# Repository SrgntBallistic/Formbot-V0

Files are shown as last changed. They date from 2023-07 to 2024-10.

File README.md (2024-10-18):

# Formbot-V0

Details/Documentation for the Formbot V0 Kit

## Detailed Review

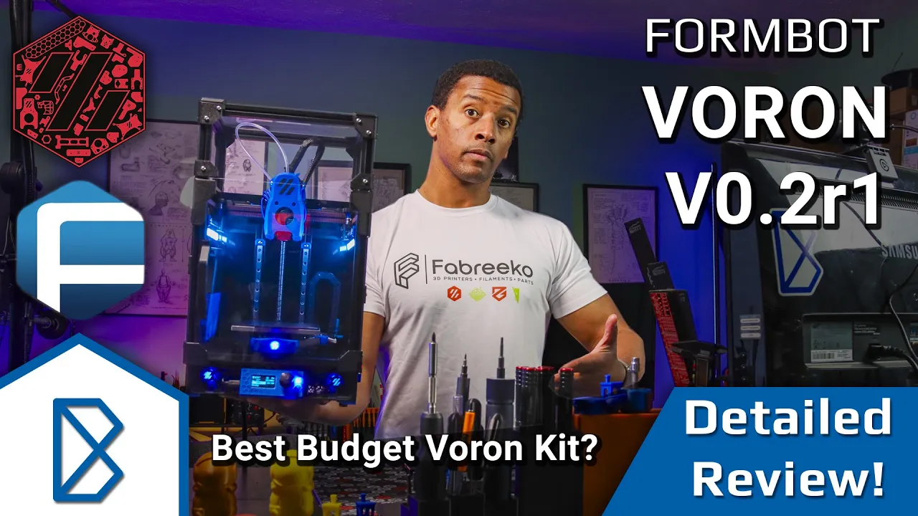
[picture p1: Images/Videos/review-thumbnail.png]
Formbot V0 Kit Review (https://www.youtube.com/watch?v=wvUrcIFF510)

<https://www.youtube.com/watch?v=wvUrcIFF510>

## Stream Series

Check out my full build stream series here:
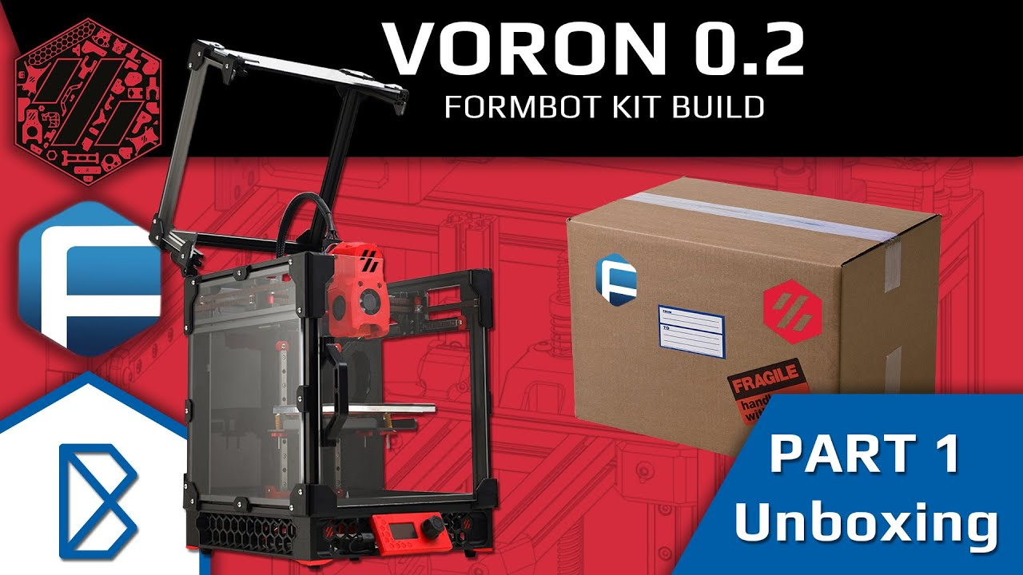
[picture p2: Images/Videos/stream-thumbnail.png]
Formbot V0 Kit Stream Series (https://www.youtube.com/playlist?list=PLwWNdxHVFVf1DbI2nGngUB0O9TWeXn2Sx)

<https://www.youtube.com/playlist?list=PLwWNdxHVFVf1DbI2nGngUB0O9TWeXn2Sx>

## Voron DB Entry

Voron DB Entry (https://vorondb.com/printer/V0-3207)
<https://vorondb.com/printer/V0-3207>

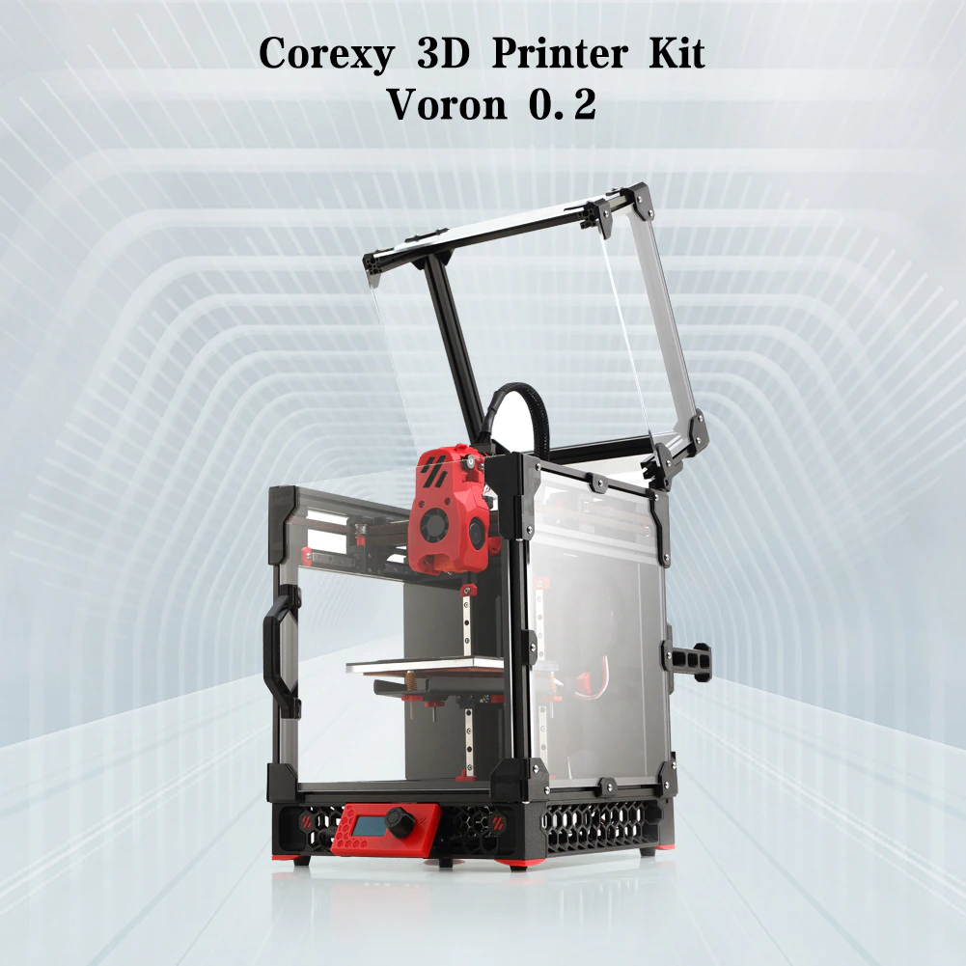
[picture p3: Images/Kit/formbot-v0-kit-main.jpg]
Formbot V0 Kit


## Features

Note: For each of the features/mods please make sure to go to the repective documentation to download and print all of the necessary STLs.

- Kirigami Bed Frame
- BTT Pi V1.2
- BTT SKR Pico
- BTT V0 Display
- CHC V6 Hotend (Upgradeable to Dragon/HF)
- Double Sided PEI Sheet
- Crimped Wiring Looms
- Moons Motors
- Stainless Steel Rails
- MIC6 Cast Aluminum Build Plate
- Polycarbonate Panels
- Gates Belts
- Vivedino 60W Silicone Bed Heater
- Stainless Steel Hardware
- Umbilical Board + Harness
- **NOT** Makerbeam XL Extrusion!!! LDO Style
- Meanwell 150W PSU

Aliexpress Listing: <https://s.click.aliexpress.com/e/_Dk19GYN>

Formbot Listing: <https://www.formbot3d.com/products/voron-v02-corexy-3d-printer-kit-with-high-quality-parts?DIST=RkFPFVk%3D>

Disclaimer: Purchases made through some store links may provide some compensation to Ballistic Tech.

## Helpful info

Most of this is set in the `printer.cfg` file I've provided:
<https://github.com/SrgntBallistic/Formbot-V0/blob/v0.2/Firmware/bigtreetech-skr-pico-v1.0.cfg>

Replace the entire contents of your `printer.cfg` file with the contents of the file linked above. Follow the instructions in the comments to add the serial Ids for your MCU and Display.

### My Config Backup

** WARNING: ** I do not advice copying my entire config setup. I'm using a lot of custom macros and plugins. I do not guarantee this config is in a working state!

<https://github.com/SrgntBallistic/blue-v0.2-backup-config>

### Motor Models

Helpful for the Autotune TMC Klipper Plugin

- A/B - MS14HS5P4150-11
- Z - LE174S-T0808-200-0-S-065
- E - CSE14HRA1L410A-01

Link: <https://github.com/andrewmcgr/klipper_tmc_autotune>

### Max Motor Currents

- A/B - 1.5A
- Z - 0.65A
- E - 1.0A

### Motor drawings with current ratings

A/B - <https://github.com/SrgntBallistic/Formbot-V0/blob/v0.2/Images/Motors/a-b-motors-drawing.jpg>

Z - <https://github.com/SrgntBallistic/Formbot-V0/blob/v0.2/Images/Motors/extruder-motor-drawing.jpg>

E - <https://github.com/SrgntBallistic/Formbot-V0/blob/v0.2/Images/Motors/extruder-motor-drawing.jpg>

### 65% Run Currents

Voron recommends 60-70% (0.6-0.7) to start
I chose 65%. Increase as needed but try to stay below 80-90%

Run Current = rated_motor_current x 0.707 x 0.65

Plug the max currents above into the equation with your desired percentage

- A/B - 0.65 x 0.707 x 1.5A = 0.69 (NICE!)
- Z - 0.65 x 0.707 x 0.65A = 0.3A
- E - 0.65 x 0.707 x 1.0A = 0.46A

### Thermistors

- Formbot Bed - "Generic 3950"
- Formbot V6 CHC Hotend - "ATC Semitec 104NT-4-R025H42G"
- Check Klipper docs for the correct sensor type based on your thermistor/hotend

### Extrusion Identification

All of the extrusions in the Formbot V0 kit are tapped on both ends. This means that using the V0 Manual extrusion identification diagrams can be a bit confusing. For 4 sets of extrusions where the manual differentiates them by tapped ends, you can consider those extrusions to be identical.

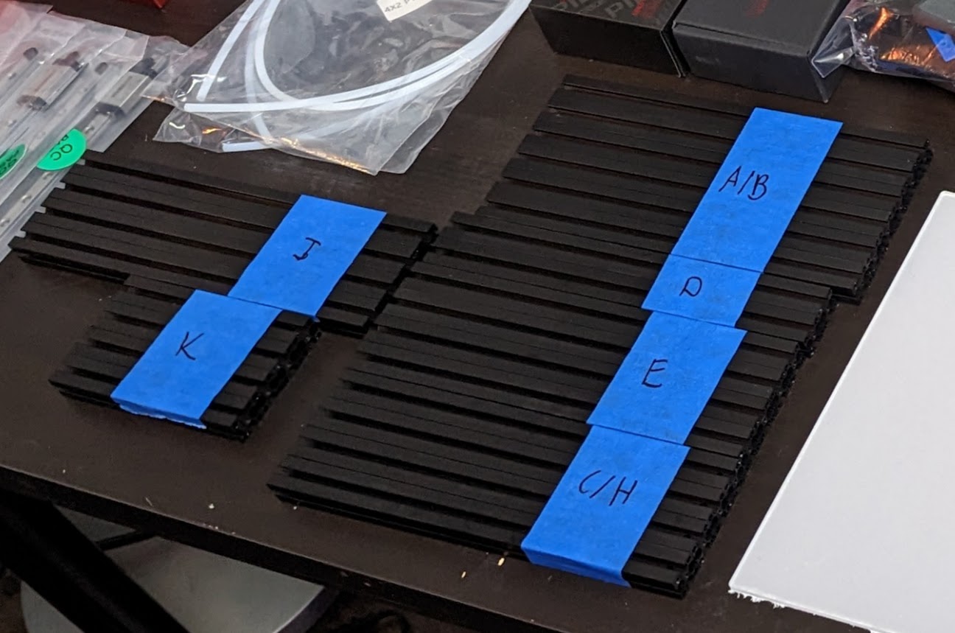
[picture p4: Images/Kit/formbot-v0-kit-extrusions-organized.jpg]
Extrusions Identification


#### Identical Extrusions

- A/B
- C/H

### No Drop Nuts

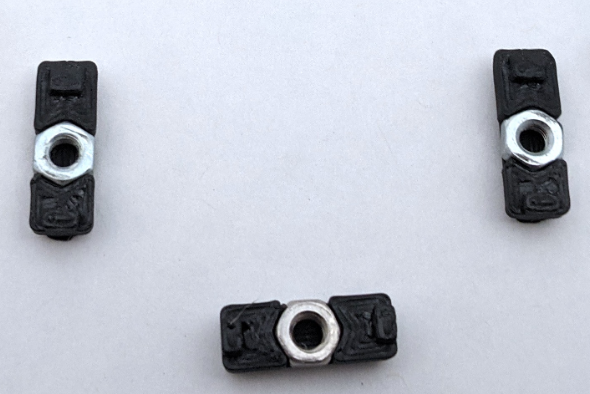
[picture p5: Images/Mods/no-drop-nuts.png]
No Drop Nuts


No drop nuts are very helpful for preventing preloaded M3 Hex Nuts from sliding around or falling out of the frame during assembly. They also allow you to pre align the nuts and hold them in place while you attatch parts to the frame.

The Formbot Extrusions are NOT MakerBeamXL profiles. They are closer to LDO's 1515 Extrusion. As such the no drop hex nut mods designed for LDO's kits work well with the Formbot kit.

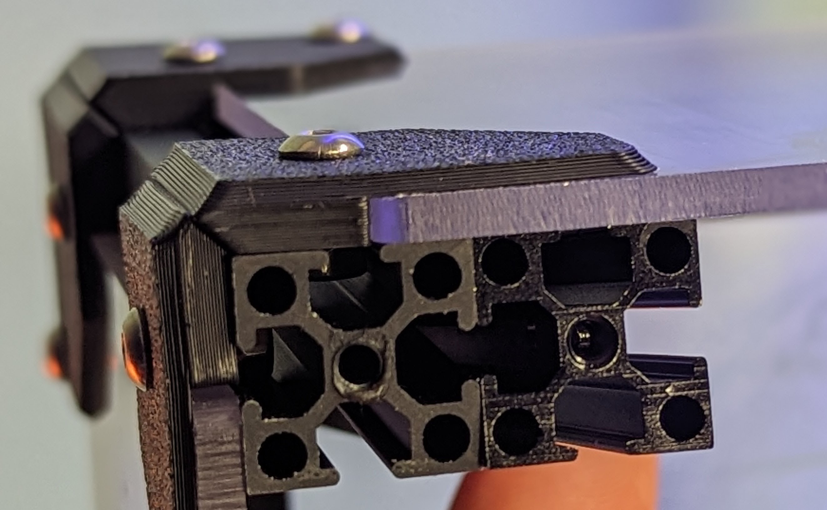
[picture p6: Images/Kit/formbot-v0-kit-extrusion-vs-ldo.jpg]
Formbot vs LDO Extrusion

Above: Left - Formbot Extrusion, Right - LDO Extrusion

#### Be Careful

I used them and found them very helpful. One big thing to note is that using the normal no drop nuts for the magnetic door latch can cause an issue. The spacing for these printed parts is such that using no drop carriers will cause them to be too far apart.

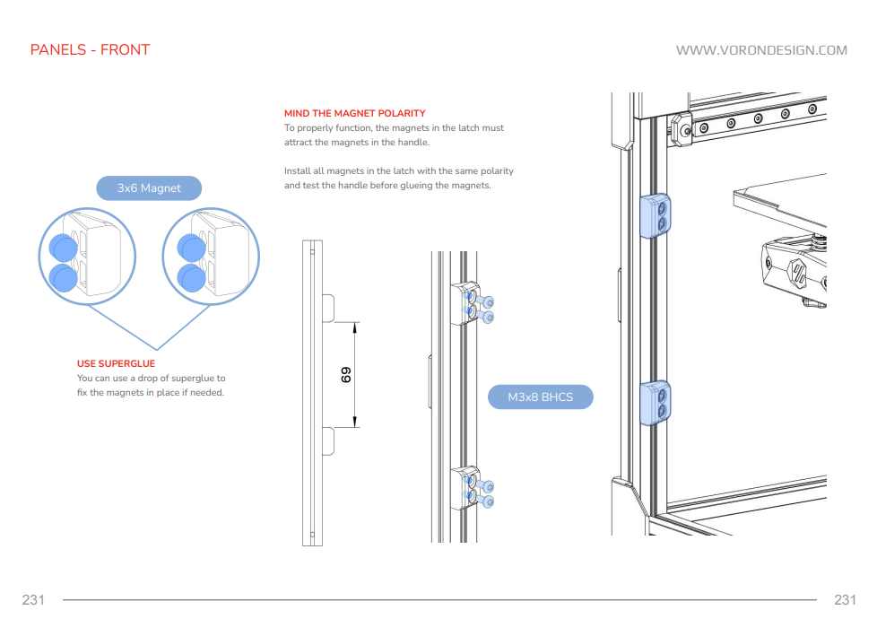
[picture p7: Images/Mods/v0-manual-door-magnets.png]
V0 Manual Door Latch


I used normal no drop nuts for these and had to essentially break apart the nut carriers to have them align with magnetic door latch parts.

There is a specific version of the No Drop Nut that is designed to be used here:

<https://github.com/VoronDesign/VoronUsers/blob/master/printer_mods/zruncho/V0_No_Drop_Nuts/stl/NoDropNut_Door_Latch_x2.stl>

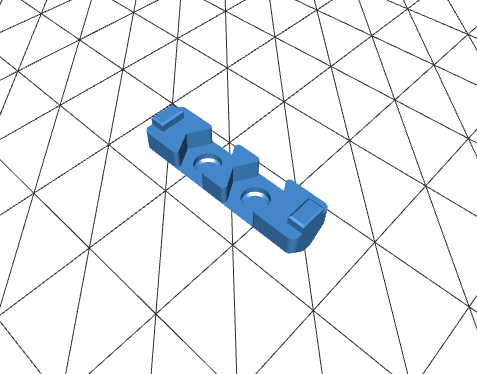
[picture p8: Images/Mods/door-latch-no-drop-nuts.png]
Door Latch No Drop Nuts


## Kirigami Bed

Kirigami Bed
GitHub: <https://github.com/christophmuellerorg/voron_0_kirigami_bed>

Manual: <https://github.com/Kagee/kirigami-bed-manual>

LDO Kirigami Docs: <https://www.ldomotion.com/p/guide/18295873486461670>

Remixed Formbot V0.2 Kirigami Frame Nutblock By @manisto: <https://www.printables.com/model/837960-kirigami-bed-nut-block-for-voron-v02>

Remixed Formbot V0.2 Kirigami Frame Chain Mount: **User Deleted. Need New Model**

The Formbot kit only comes with the Kirigami Frame. There's no LED/PCBs/Wago connectors, etc... included with the kit. You can source these yourself, find a partial wiring kit that includes them, or just leave them out and hard wire the bed components. See my My Mods section for the kit I bought.

The Kirigami bed frame is a great mod/upgarde that comes with the kit. It replaces multipe extrusions and printed pieces with a single rigid bed frame. The LDO Docs and Kirigami manual by Kagee provide some great info on general installation of the bed.

I had some trouble with the provided bed. I was able to get through all the issues with small DIY fixes. Other people have also noted they've run into these issues on the Voron Discord as well as the Kirigami GitHub. YMMV

## Issues

- Frame Thickness
  - My frame measured about 2.3-2.5mm
    - I think this is due to the thickness of the paint on the frame
  - Spec is 2mm, max tolerance of 0.2mm
  - Caused the frame to not fit the printed Kirigami "stealth" Parts
    - Stealth Nut Block
    - Steath Chain Mount
    - Can file the gaps in these parts or modify them in CAD and reprint if they don't fit
    - Can also use some of the legacy non stealth parts

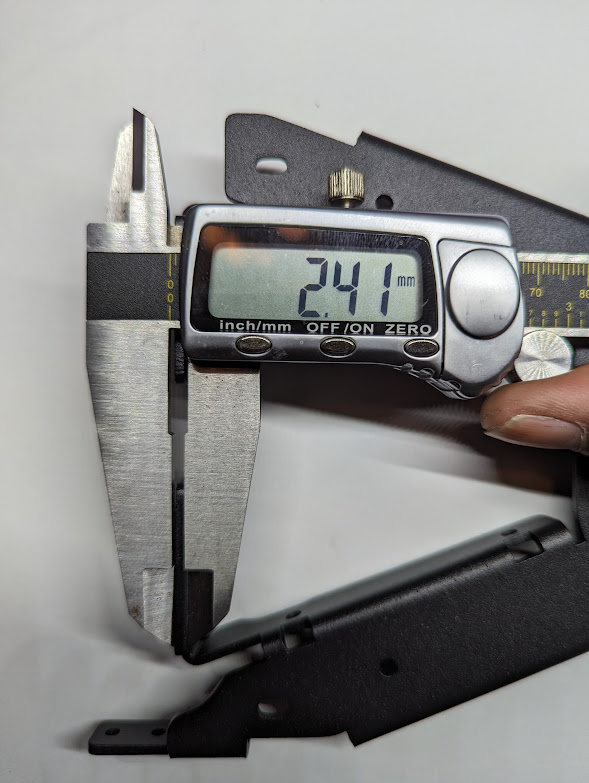
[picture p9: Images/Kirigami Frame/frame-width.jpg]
Kirigami Frame Thickness


For the chain mount Voron Discord/Printables user Tommy Vercetti remixed the part so it fits well on the Formbot frame

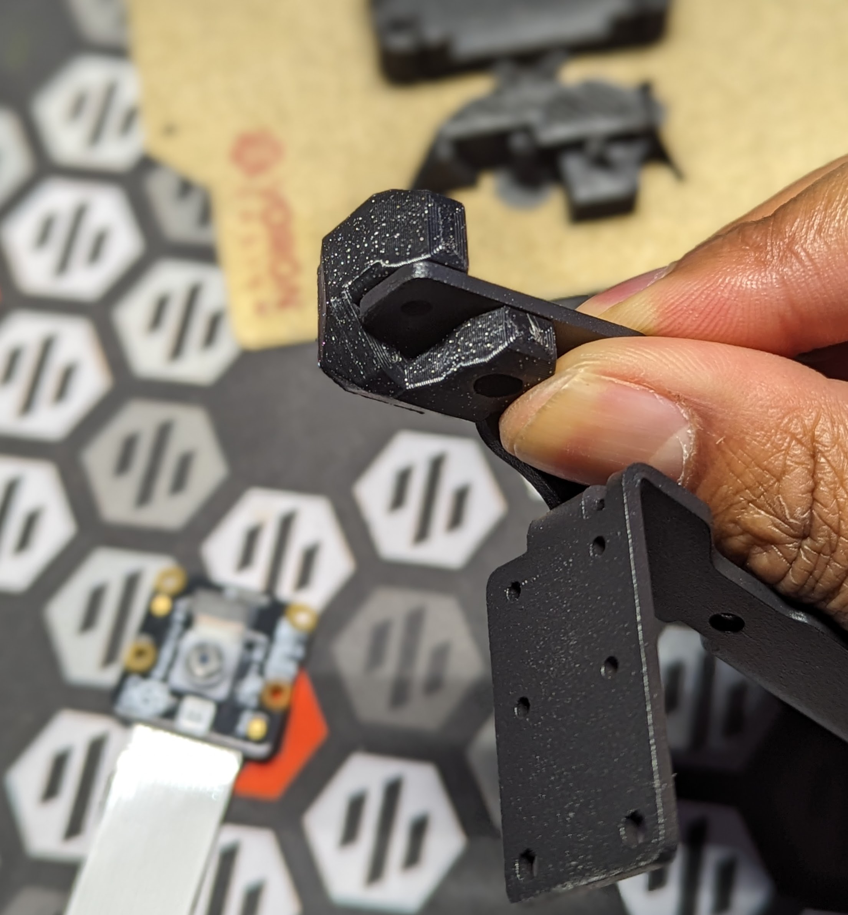
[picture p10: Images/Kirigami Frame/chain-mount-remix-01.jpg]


GitHub Issue: <https://github.com/christophmuellerorg/voron_0_kirigami_bed/issues/16>

- Frame holes
  - Again likely due to the thickness of the paint
  - Caused some slight over constraining of the frame when attached to the Z carriages
  - My mounting screws barely fit through the holes
  - No wiggle room to allow the frame and carriages to self align in a well enough that the frame and carriages would fall under their own weight
    - Didn't completely bind the frame movement
    - Just wasn't as smooth/free as after fixing
  - Compounded with the frame not fitting in the nut block well
  - Solved by filing out the holes in the frame
    - This reduced the constaining and allowed the bed to fall easily

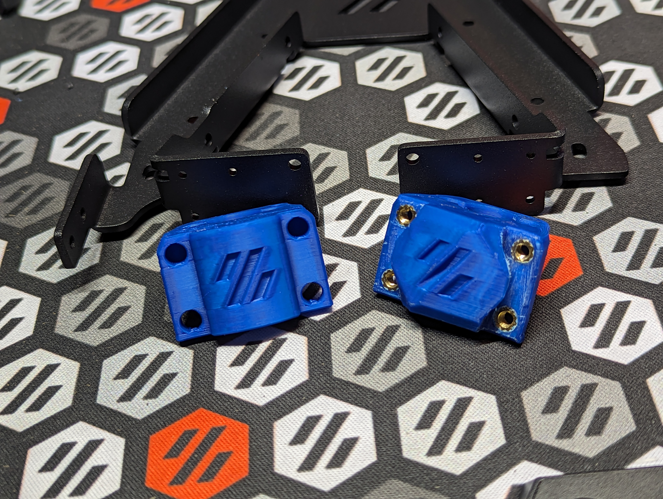
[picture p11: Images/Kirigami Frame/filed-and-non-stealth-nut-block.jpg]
Kirigami Frame Nutblocks


Non Stealth (Left) and Filed Stealth Nutblock (Right)

- Thermal Fuse Location
  - When I went to adjust the bed screws so they bed was just close enough to the nozzle I couldn't get the bed springs to compress enough
  - The thermal fuse was running into the frame
  - I could have reduced the Max Z so the bed wouldn't come up as high after homing
  - But didn't want to lose any Z height
  - Solved by filing away a tiny bit of material on the frame where the fuse was interferring

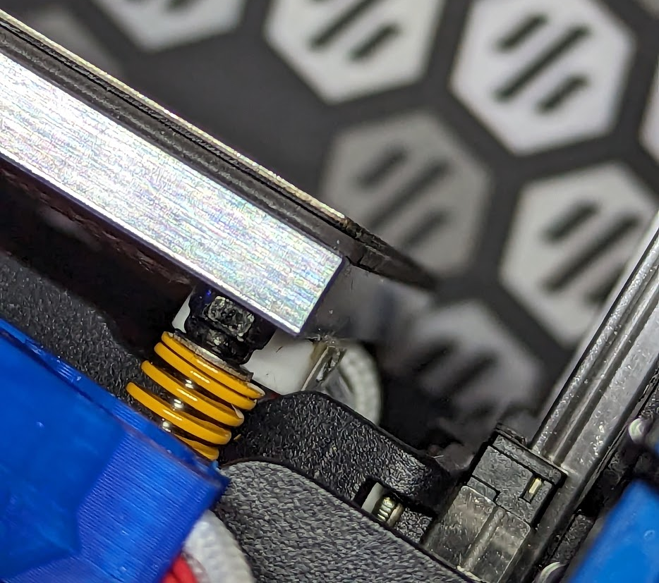
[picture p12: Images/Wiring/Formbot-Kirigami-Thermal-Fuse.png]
Thermal Fuse interference


There are mounting slots in the Kirigami frame that allows forward/backward movement of the bed screws. The LDO Docs include a link to a set of spacers that allow locking the heated bed in the forwardmost or rear most position.

Position these such that the nozzle is able to reach the full extent of the front and back of the bed. For me that was with the bed towards the rear.

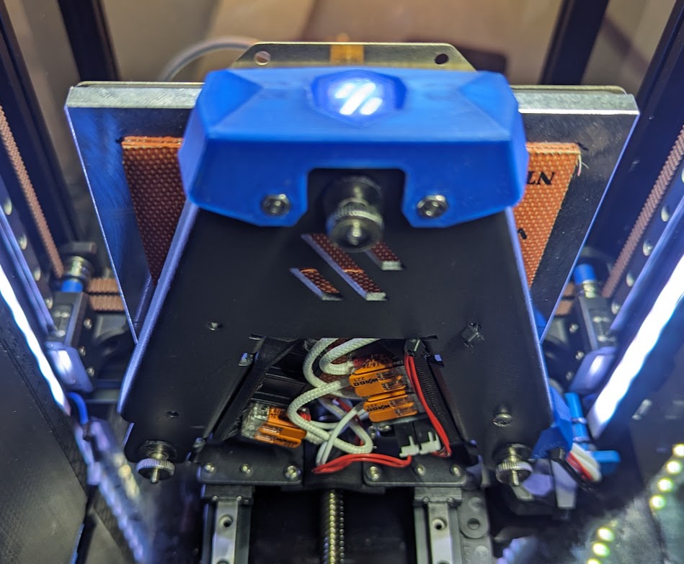
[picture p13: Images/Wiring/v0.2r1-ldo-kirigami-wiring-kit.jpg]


## BTT SKR Pico

GitHub: <https://github.com/bigtreetech/SKR-Pico>

Manual: <https://github.com/bigtreetech/SKR-Pico/blob/master/BTT%20SKR%20Pico%20V1.0%20Instruction%20Manual.pdf>

**Flashing (From Pi without PC)**: <https://docs.vorondesign.com/build/software/skrPico_klipper.html>

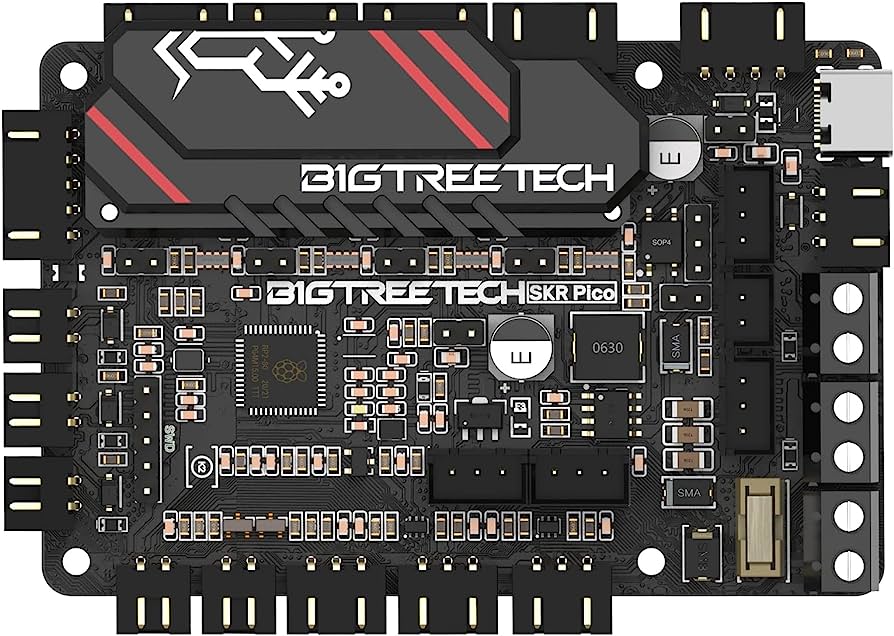
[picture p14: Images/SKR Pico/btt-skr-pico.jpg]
BTT SKR Pico


The SKR Pico is a nice small footprint Main Board. It trades some IO/connectivity capability for its compact size. Ex: there's no input of the chamber thermistor that comes on the V0 Umbilical frame PCB. Also there's no extra fan ports to hook up fans for something like the Nevermore filter. An Extra MCU like the Klipper Expander would be necessary to get some of this IO back.

### SKR Pico Compile Params

There's some new compile params for the RP2040 in Klipper MenuConfig. Here's what worked for me

- MCU: Raspberry Pi RP2040
- Bootloader Offset: No bootloader (for USB, 16Kib for Canbus)
- Flash chip: W25Q080 with CLKDIV 2
- Communication interface (USB)
- USB IDs: USB Serial number from CHIPID
- GPIO pins: Empty

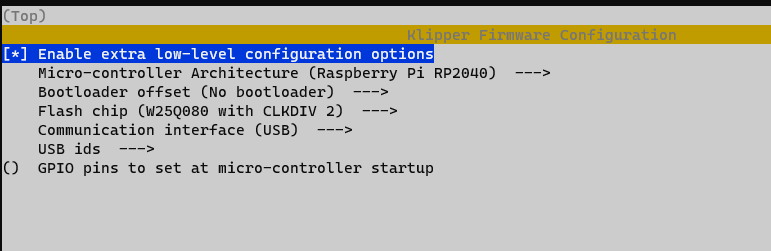
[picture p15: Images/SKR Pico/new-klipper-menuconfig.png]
BTT SKR Pico Menuconfig


## BTT V0 Display

GitHub: <https://github.com/VoronDesign/Voron-Hardware/tree/master/V0_Display>

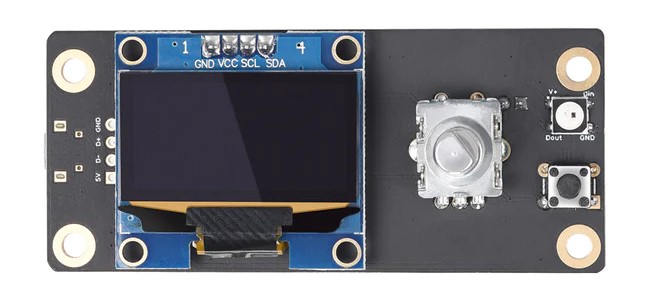
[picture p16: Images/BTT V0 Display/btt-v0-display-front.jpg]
V0 Display


Flashing Docs: <https://github.com/VoronDesign/Voron-Hardware/blob/master/V0_Display/Documentation/Setup_and_Flashing_Guide.md>

Biqu Listing: <https://biqu.equipment/products/voron-display-v1-0>

Ali Express Listing: <https://s.click.aliexpress.com/e/_DBvhC7R>

Features:

- 1.3" OLED Display
- Rotary Encoder
- Neopixel
- STM32F042F6P6 MCU
- USB Connector

Small simple display with a neopixel onboard to change the LCD Color.

### Fixing OLED Lines/Smears

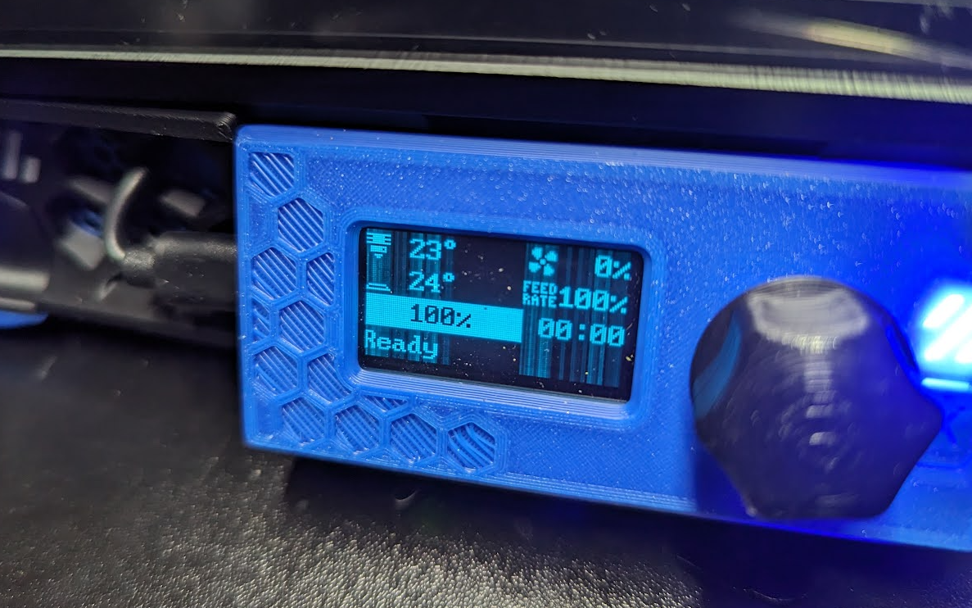
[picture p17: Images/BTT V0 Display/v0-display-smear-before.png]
V0 Display with Smear


Some OLED displays can have a bit of a "smearing" effect on them. There is a line in the `[mcu display]` section of the config you can uncomment and modify to help with that. Timmit the developer of the V0 Display recommends a value of 31 (0 is the default).

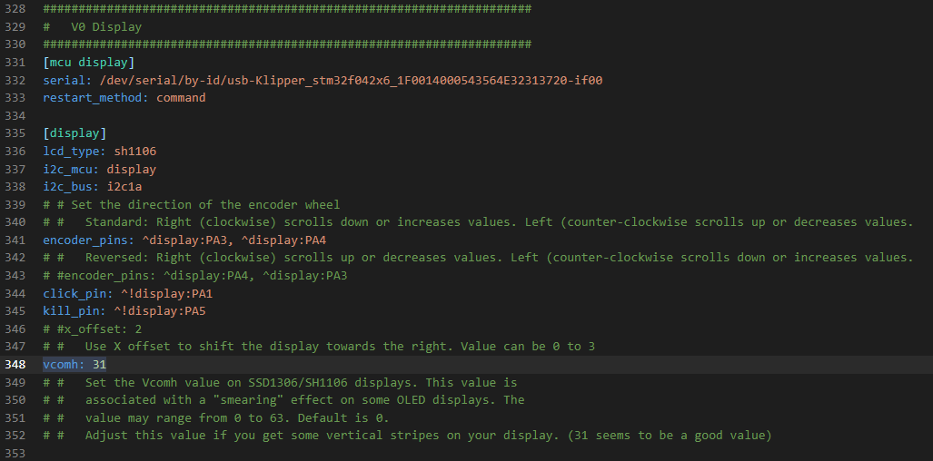
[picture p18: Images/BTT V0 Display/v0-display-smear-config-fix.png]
V0 Display Smear Config Fix


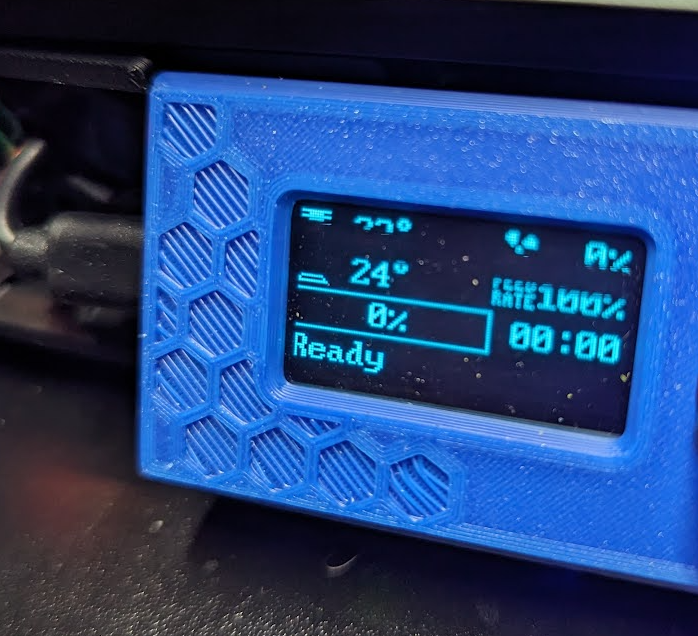
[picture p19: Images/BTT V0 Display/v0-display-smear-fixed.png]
V0 Display Fixed


## BTT Pi V1.2

GitHub: <https://github.com/bigtreetech/BTT-Pi>

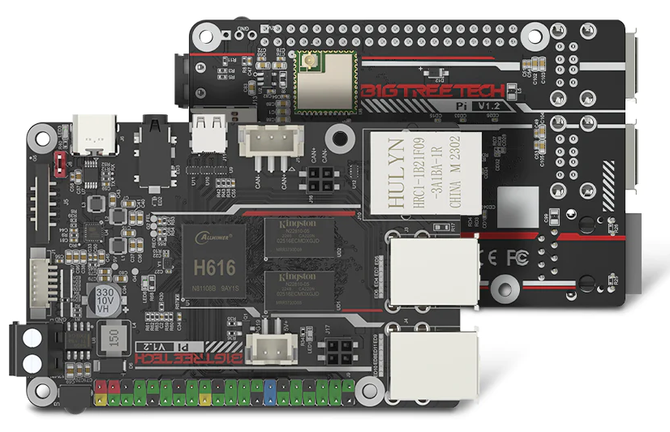
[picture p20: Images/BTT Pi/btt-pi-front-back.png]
BTT Pi V1.2


Manual: <https://github.com/bigtreetech/BTT-Pi/blob/master/BIGTREETECH%20Pi%20V1.2%20User%20Manual.pdf>

Biqu Listing: <https://biqu.equipment/collections/control-board/products/bigtreetech-btt-pi-v1-2>

Aliexpress Listing: <https://s.click.aliexpress.com/e/_DmQwZ0V>

Useful features:

- ADXL SPI Port for Input Shaping
- 12-24V Power terminal input
- 5V USB-C Power input

The BTT Pi V1.2 is a nice alternative to Raspberry branded Single-Board-Computers that have frequently shot up in price. It has some nice 3D Printing specific features and numerous ways to power it.

### Flashing Image

The BTT Pi uses the same images as the BBT CB1 compute module. You can follow instructions for installing it.

BTT has 2 versions of the Kernal. A Minimal image and a Klipper image. The Klipper image has Klipper, Mainsail, Crowsnest and most other dependencies pre-installed. They just need to be updated after.
Images: <https://github.com/bigtreetech/CB1/releases>

By Default the host name for the image will be "btt-cb1" and it can be accessed with "btt-cb1.local" if you don't know the IP Address for it yet.

## V0 Umbilical

GitHub: GitHub: <https://github.com/VoronDesign/Voron-Hardware/tree/master/V0-Umbilical>

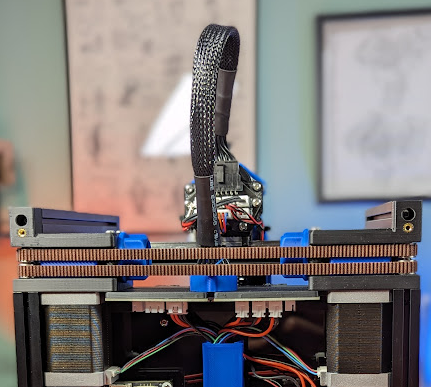
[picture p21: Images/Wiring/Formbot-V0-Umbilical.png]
V0 Umbilical


The V0 Umbilical is a great mod included in this kit. It makes wiring much easier. All of the signals/power to the toolhead goes through a toolhead PCB breakout board, down to the back of the frame via a pre-made wire harness, through a second frame pcb breakout board and finally down to the SKR Pico.

Formbot has precut and crimped most of the wires that go from the mainboard to the frame PCB. They've also made most of the wires that hook into the toolhead pCB the correct length as well.

Be sure to print the V0 Toolhead PCB mount and strain relief found here:
<https://github.com/VoronDesign/Voron-Hardware/tree/master/V0-Umbilical/STLs/V0.2>

## Wiring

### General Wiring

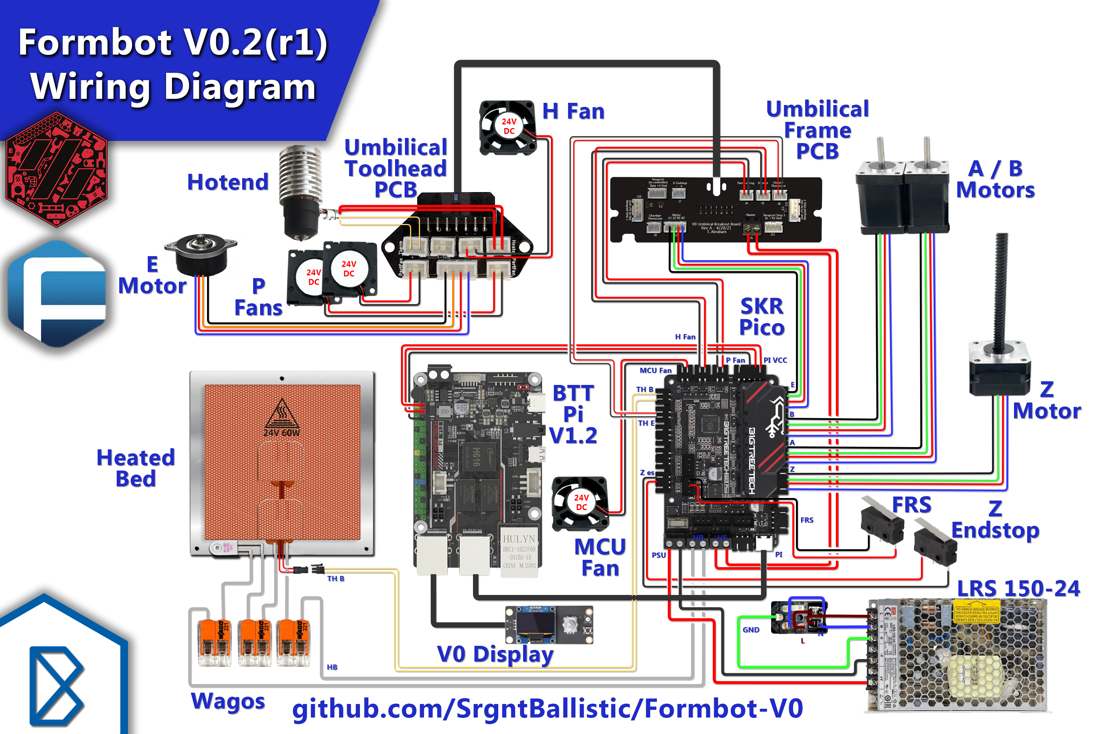
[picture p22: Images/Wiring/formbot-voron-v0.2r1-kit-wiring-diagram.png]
Stock Formbot V0.2(r1) Wiring Diagram


This is a general wiring diagram for a Formbot V0.2(r1) kit. The only thing specific to the `V0.2r1` is the Filament Runout Sensor (FRS) which gets plugged into the `E0 Endstop` input on the SKR Pico (next to the RGB/Neopixel). Otherwise it should serve pretty well as a general `V0.2` build.

Since the `V0.2` uses sensorless homing on the X-Y/A-B axes there's no endstops plugged into either of those inputs. In fact it's important to ensure that nothing is plugged into these inputs. Otherwise sensorless homing will not work.

** Note: ** Use this wiring diagram as a guide, but be sure to follow the polarity from the SKR Pico all the way up to the Umbilical PCB and out of the Toolhead PCB. I highly recommend using a multimeter to check for continuity of the pos/neg at the board and toolhead PCB. Some fans or intermediate wires ** MAY ** be pinned backwards. If this is the case I suggest depinning the connector and swapping the wires to ensure the correct polarity is carried all the way up to the fans.

There is no polarity for thermistors or heaters!

### Kirigami Bed Wiring

The Formbot kit does **NOT** include any wago or inline connectors!

The Kirigami Bed Frame alows splitting the wiring coming out of the bed so that the bed can be removed and worked on without being tethered to the printer.

Voron recommends using Wago connectors to allow easily disconnecting the wires. The Kirigami bed mod includes mounts for the Wago connectors.

Since the Formbot kit bed heater doesn't include an integrated thermal fuse it needs to be connected inline with one side of the bed wires.

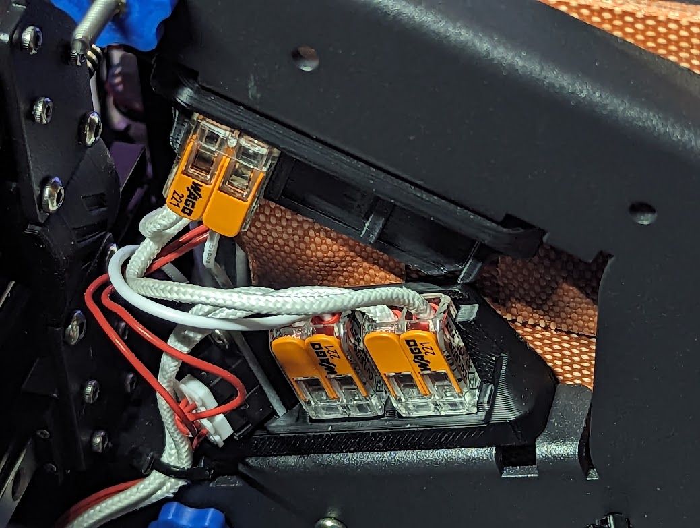
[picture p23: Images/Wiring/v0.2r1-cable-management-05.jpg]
Bed Wiring


### Generic Formbot Wiring

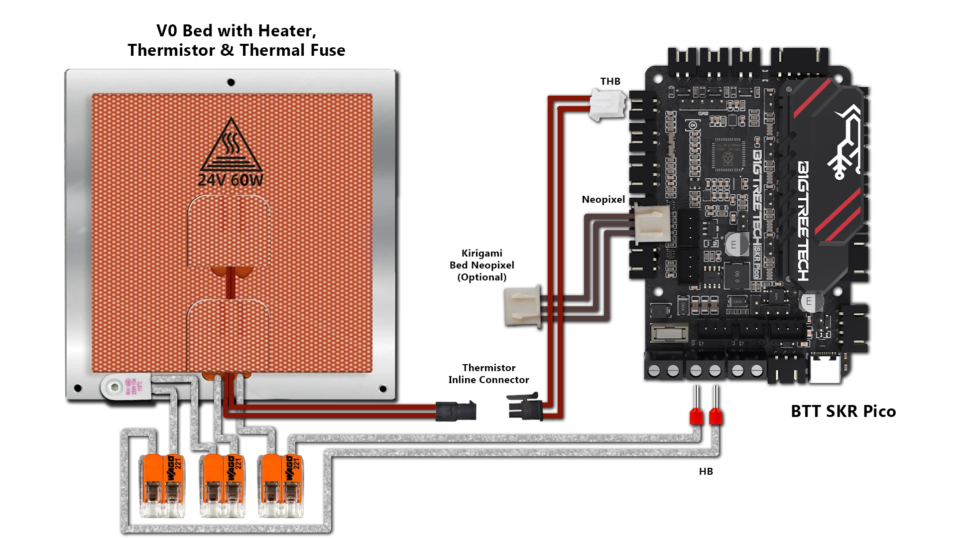
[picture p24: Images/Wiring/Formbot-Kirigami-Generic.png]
Generic Formbot Kirigami Wiring


An inline connector can be used to split the Thermistor wires under the bed.

** NOTE: User [@Carlsans] (https://github.com/Carlsans) mentioned his Formbot kit came with a preinstalled [thermal fuse] (https://github.com/SrgntBallistic/Formbot-V0/issues/3)

### Formbot Wiring + LDO Kirigami Wiring Kit

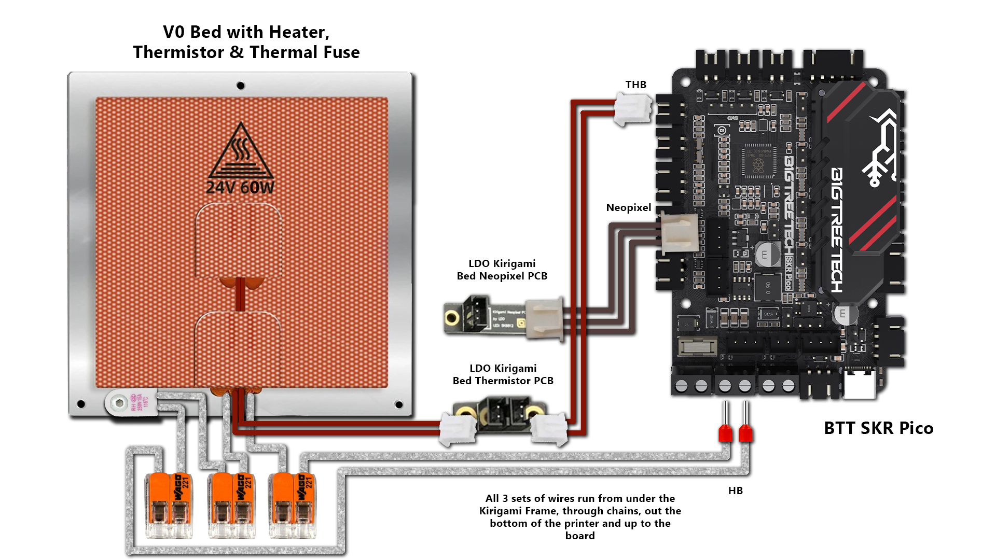
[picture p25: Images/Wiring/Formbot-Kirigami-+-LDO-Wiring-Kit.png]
Generic Formbot Kirigami Wiring


The LDO wiring kit includes 2 Wago mounts, a Thermistor breakout PCB and an LED PCB. A third wago is needed for the Formbot Thermal Fuse. The LDO V0 repo has stls for mounting its PCBs and the wagos. See the Kirigami Manual for more info.

### BTT Pi Power

Formbot provides a precut, pre-crimped wire harness to go from the BTT SKR Pico's top right pins over to the BTT Pi V1.2's VCC and GND GPIO Pins. It provides 2 5V wires and a single ground. I think these were design to work with an original Raspberry Pi 3/4 which has it's GPIO on the right.

Pi Power Wires Janky

Since the BTT Pi has it's GPIO on the left the only way to get the wires over to those pins I had to stretch them across both boards. I felt the looked bad and worried about the tension.

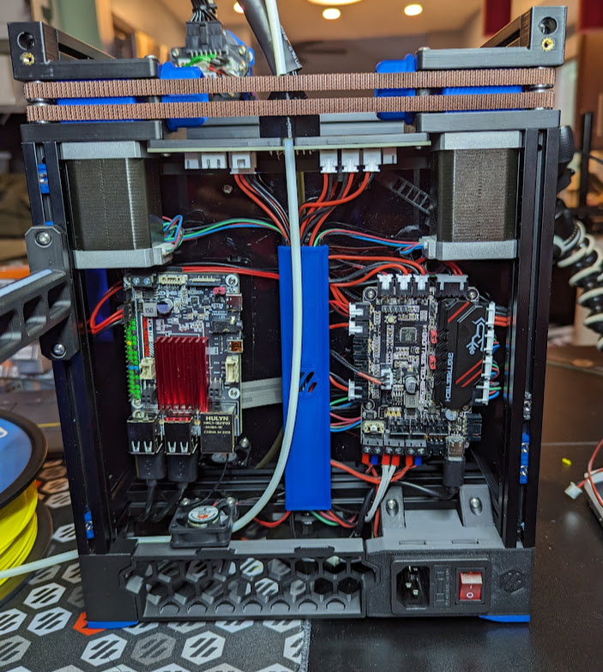
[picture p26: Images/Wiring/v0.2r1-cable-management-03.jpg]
Pi Power Fixed


To solve this I used their JST connector and repinned/crimped the some longer wires with Dupont connectors on the opposite side. With the wires longer I can pas them under the edges of the boards and through the cable management channel in the middle

### BTT Pi to BTT SKR Pico Uart Communication

By default the Formbot kit connects the BTT Pi and SKR Pico by USB cable. This works well and is easily set up. However, it does limit the number of open USB ports to two (one is also taken up by the V0 Display). Since I also added a Klipper Exander and USB camera that meant all four ports were used. Leaving none for things like a USB Input Shaper Accelerometer.

Connecting the Pico and Pi via UART opens up a spare port again to help with this.

As noted in the section above the Formbot kit powers the the Pi via two +5V and a single GND set of wires going from a JST port on the SKR Pico to the GPIO Pins on the Pi. This is actually the UART comms header on the SKR Pico so we can easily add two wires (Green and Yellow in the Wiring Diagram) to free up the USB Port.

One end needs to be crimped with a JST XH connector and the other needs to be female duponts. Since this will only be transmitting data the guage isn't hugely important. You can use already crimped female-to-female Dupont bread board wires cut to size and crimped with a JST on one end. OR in my case take a pre-crimped JST wire and crimp a Dupont (harder to crimp) connector to the other end.

Then plug the extra two wires into the 5 pin JST connector housing on one end, and the Dupont connects onto the pins adjacent to the power pins on the Pi GPIO.

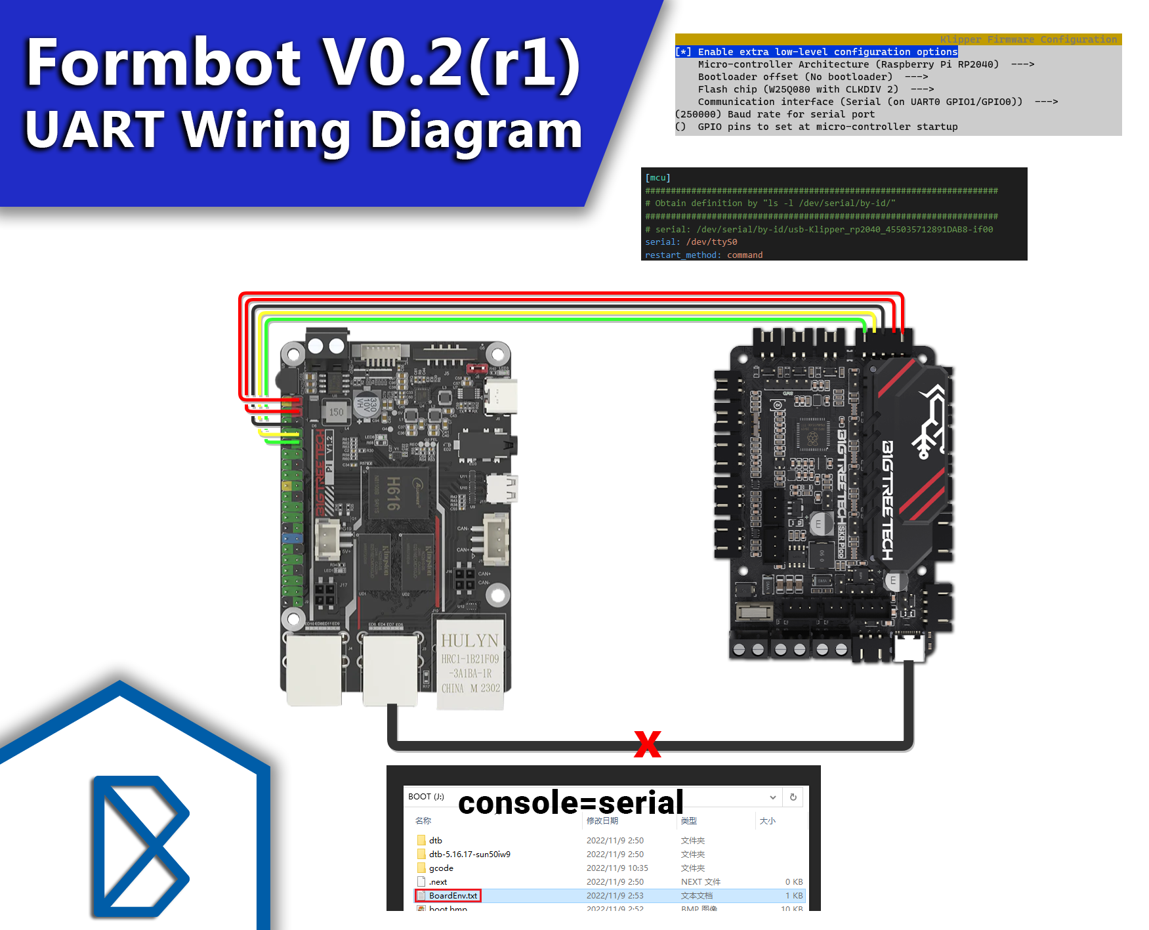
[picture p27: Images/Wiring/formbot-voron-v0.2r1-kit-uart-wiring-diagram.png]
UART Wiring


You'll need to shut down the Pi remove the SD Card, plug it into a computer and open the `BoardEnv.txt` file on the boot sector of the card. In that file change the line with `console=`and set it to `console=serial` to tell the Pi to talk via it's UART interface.

From there you can put reconfigure the Pico firmware to use `UART0 GPIO1/GPIO0` for it's communication interface. Flash it via USB. Disconnect the USB and connect it via the new UART cable. Finally in your `printer.cfg` change the `serial:` portion of the MCU definition to `/dev/ttyS0`.

You should then be able to reboot the Pico and communication between the board and the Pi should work as normal

## Products Used

### Phaetus Dragon HF

This is an optional upgrade on some Formbot listings. It offers single hand nozzle tightening and much higher Max Flow Rate compared to the default Formbot V6 CHC nozzle.

**Ali** - <https://s.click.aliexpress.com/e/_DlBBu2d> You have to buy all the parts separately...

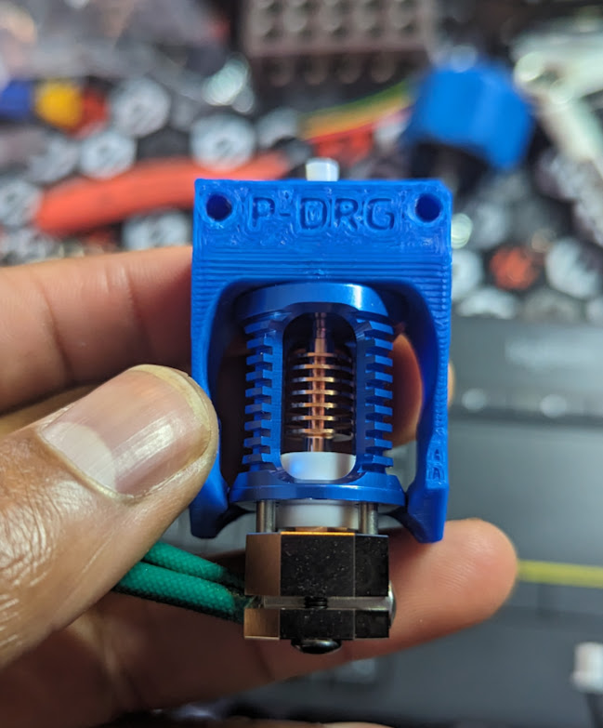
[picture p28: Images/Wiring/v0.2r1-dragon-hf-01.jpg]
Dragon HF


### Bondtech 0.4 CHT Nozzle

This further increases the flow rate of the Dragon HF.

**MatterHackers** - <https://www.matterhackers.com/store/l/bondtech-cht-m6-nozzle/sk/MEH3UZ0N?aff=7617>

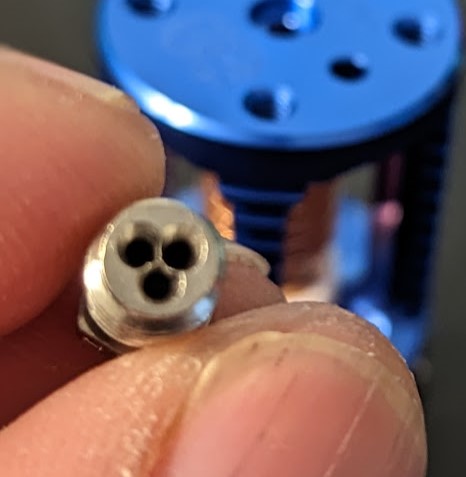
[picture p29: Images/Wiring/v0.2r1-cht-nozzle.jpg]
CHT Nozzle


### Fabreeko cPIF V0.2 Printed Parts

**Fabreeko cPIF**: <https://www.fabreeko.com/collections/v0/products/voron-v0-2-s1-printed-parts-by-pif?variant=43678271570175>

I found the cPIF parts pretty nice. I've since replaced a couple of of failed parts but I don't attribute the failures to the quality of the prints. More to some inherent issues in the part design

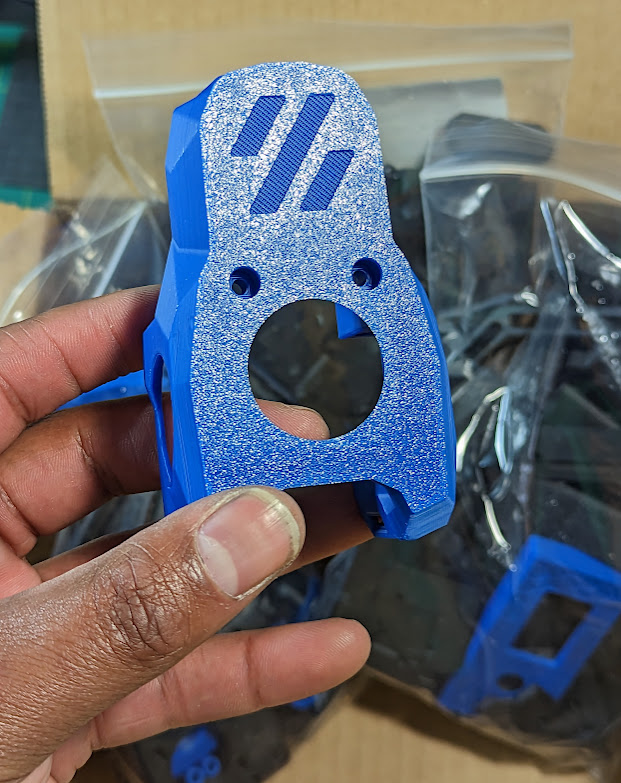
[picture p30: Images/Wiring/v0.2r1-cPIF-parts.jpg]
cPIF Parts


### EP2 Grease

**Product Links**:

- **Fabreeko Grease**: <https://www.fabreeko.com/collections/v0/products/mobilux-ep2-grease>
- **KB3D Grease**: <https://kb-3d.com/store/tools-equipment/497-linear-rail-carriage-lubrication-kit-mobilux-ep2-20ml-1645909620080.html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>
- **West3D Grease**: <https://west3d.com/products/mobil-mobilux-ep2-10ml-filled-syringe-with-blunt-tip>

I originally greased the rails with White Lithium lubricant but bought this and regreased them when I redid the frame.

### GDS Time Fan Mini Stealthburner Fan Kit

- **DFH Fan Kit**: <https://dfh.fm/products/voron-mini-stealthburner-fan-kit?_pos=7&_sid=66ce4f1ac&_ss=r>
- **Ali 3010 Axial**: <https://s.click.aliexpress.com/e/_Dl3Eglj>
- **Ali 3010 Blower**: <https://s.click.aliexpress.com/e/_DCMx5xj>

The stock fans are probably the most noticable lower quality parts of this kit. I found the plastic a bit brittle and the leads didn't tuck into the their slots on the body. This cause them to get pinched when I put them in the Mini SB.

### RC Style Hex Drivers

I found using any type of ball end and some not very sharp edged hex/allen drivers or bits resulted in stripped screws. In particular on the Frame and rails screws which I ended up screwing and unscrewing numerous times.

I tried my RC style hex drivers which have noticably sharper corners and noticed I didn't have any stripped screws.

Most will probably work well. Fabreek sells a couple different sets

**Product Links**:

- **Fabreeko Set**: <https://www.fabreeko.com/products/fabreeko-precision-screw-driver-set-of-5?variant=38183379828934>
- **Ali 4PC Set**: <https://s.click.aliexpress.com/e/_Dn590Zb>

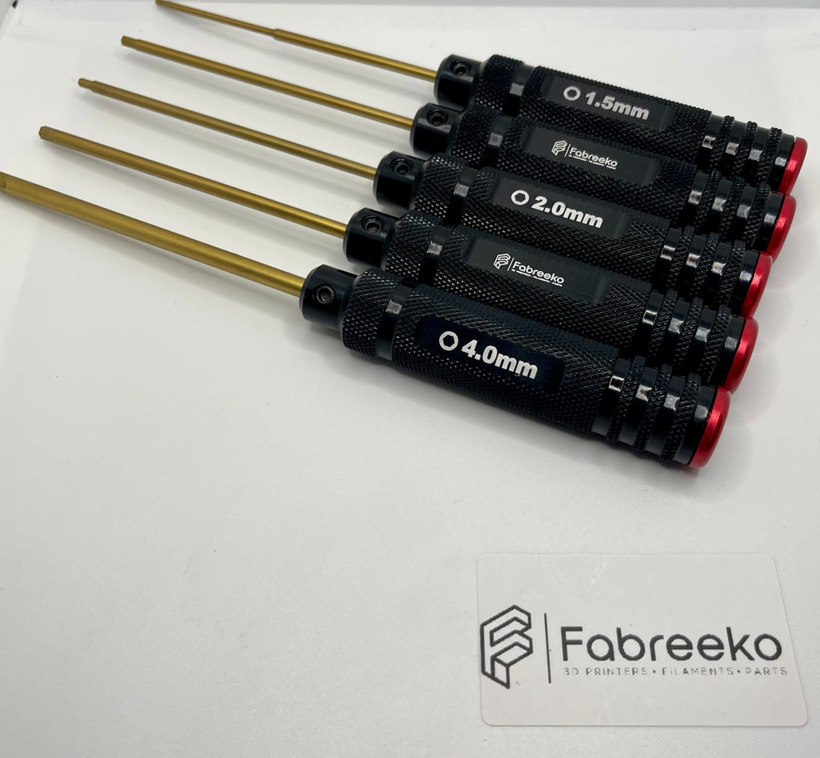
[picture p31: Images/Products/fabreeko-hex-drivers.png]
Fabreeko Hex Drivers


**Model Links**:

- **Fabreeko Driver Set Gridfinity Holder: <https://www.printables.com/model/270299-gridfinity-fabreeko-screwdriver-tool-holder>

### Flexible "Drone" USB Cable

This low profile USB cable was usefult to connect the Klipper Expander board to the BTT Pi V1.2. They can be configured with any type of end connectors. I used a 90 Degree Micro USB on one end and a standard Type A USB on the other
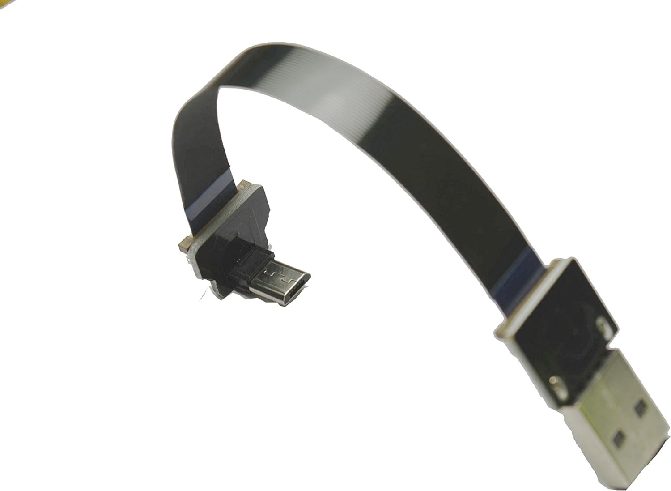
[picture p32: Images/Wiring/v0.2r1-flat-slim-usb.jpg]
Flixible USB Cable


**Ali Link**: <https://s.click.aliexpress.com/e/_DCxyxhJ>

### Ferrules

I try to use ferrules for every screw terminal whenever possible. If you don't have a ferrule set and/or crimper they're a great pickup for 3D Printer builders

**Ali Link**: <https://s.click.aliexpress.com/e/_DnPAwm9>

### USB Camera

The BTT Pi V1.2 doesn't have a traditional Pi Camera connector. I used a common ELP 4K Pi style USB camera instead. The quality is pretty clear

**Product Links**:

**Ali 4K 170**: <https://s.click.aliexpress.com/e/_DBiftLT>

**Model Link**: <https://www.printables.com/model/656391-voron-02-tophat-corner-camera-mount/>

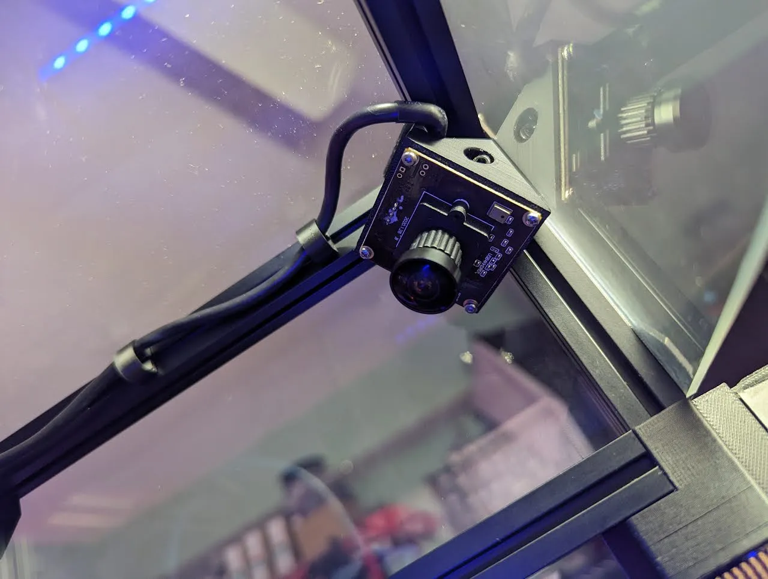
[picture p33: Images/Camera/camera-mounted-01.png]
Camera + Mount


### LDO Kirigami Wiring Kit

**Description**: "LDO Krirgami LED PCB, LDO Kirigami Breakout PCB, LDO Breakout Wire Kit, Wago 221-412 x 2 For use with Kirigami Beds"

**Product Links**:

- **DFH Kit Full Wiring Kit**: <https://dfh.fm/products/voron-v0-kirigami-bed-wiring-and-led-kit>
- **West3D Kit PCB + Wagos**: <https://west3d.com/products/v0-2-kirigami-led-and-breakout-pcb-with-wagos>
- **Fabreeko LDO Kirgami LED + PCB**: <https://www.fabreeko.com/products/v0-2-kirigami-led-and-breakout-by-shammy>
- **Ali Wagos 5Pc**: <https://s.click.aliexpress.com/e/_DB8wSuh>
- **Ali Single NeoPixel PCB**: <https://s.click.aliexpress.com/e/_DdBNT49>

Since the Formbot Kit only comes with the frame I bought this wiring kit to get close to what comes in the LDO kit.

LDO V0 Wiring Kit

### Nevermore V6

**Description**: 3D Printed Activated Charcoal Filter

**Mod Link**: <https://github.com/nevermore3d/Nevermore_Micro/tree/master/V6>

**Product Links**:

- **Fabreeko 5015 Fans**: <https://www.fabreeko.com/products/5015-blower-fan-by-honeybadger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>
- **DFH 5015 Fans**: <https://dfh.fm/products/5015-24v-dual-ball-blower?_pos=1&_sid=426120d23&_ss=r>
- **Ali 5015 Fans**: <https://s.click.aliexpress.com/e/_DBJycYD>
- **Ali 5pc Wagos**: <https://s.click.aliexpress.com/e/_DB8wSuh>
- **Fabreeko Activated Charcoal Pellets**: <https://www.fabreeko.com/products/nevermore-carbon?_pos=1&_sid=6691ede3b&_ss=r&variant=43205733449983>

Printing ABS (as with most filament materials) can release VOCs (Volatile Organic Compounds) and has a noticabley more noxious smell than other materials like PLA. An active carbon filter can help clear absorb those orders/VOCs and move some air around the chamber for more efficient heating.

### Klipper Expander Board

Board allows increased IO and power for mods and upgrades limited by BTT SKR Pico board

- Neopixels
- Nevermore Fans
- Chamber Thermistor

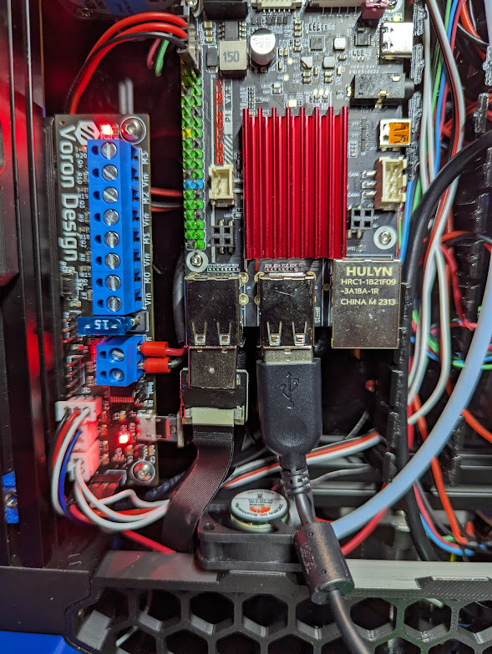
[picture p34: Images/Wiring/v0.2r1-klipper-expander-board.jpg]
Klipper Expander Board


**Product Links**:

- **Fabreeko**: <https://www.fabreeko.com/collections/v0/products/klipper-expander-board>
- **DFH**: <https://dfh.fm/products/klipper-expander-for-voron-3d-printers?_pos=1&_sid=9323da715&_ss=r>
- **Ali**: <https://s.click.aliexpress.com/e/_DdIuJM5>

### Fabreeko Honeybadger V0 Metal Toolhead Carriage

**Product Link**: <https://www.fabreeko.com/collections/v0/products/v0-2-metal-toolhead-carriage-for-v0-2-by-honeybadger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>

**Variation**: MGN7H

Requires - 4 M2x4 screws (for carriage mount), M3x8 (replaces rear M3x16 motor plate screw)

One of the parts I noticed failing was the X carriage. The hex nuts place on the front of the carriage started spinning in their slots. There was also a couple layer splits in the part when I removed it.

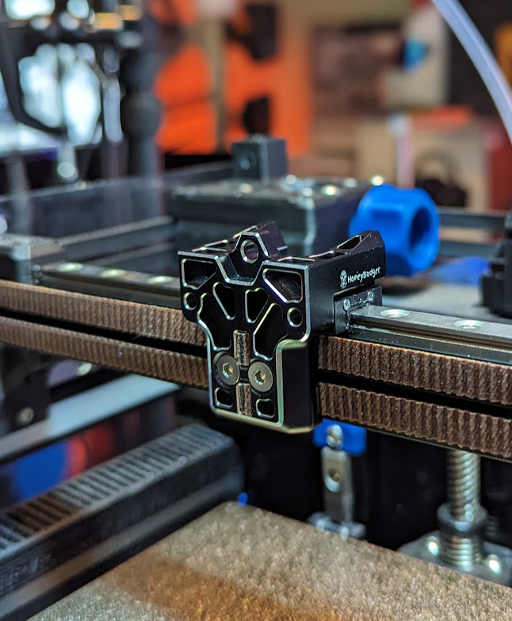
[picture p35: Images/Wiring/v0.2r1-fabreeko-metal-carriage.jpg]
Fabreeko Metal Carriage


### Rainbow Matchstick LEDs

**Product Links**:

- **DFH**: <https://dfh.fm/products/rainbow-stick?variant=43340753666270>
- **West3D**: <https://west3d.com/products/rainbow-on-a-matchstick?_pos=10&_sid=57e17111c&_ss=r>
- **Fabreeko**: <https://www.fabreeko.com/products/daylight-disco-stick-rgb?variant=43841072922879>
- **Ali**: <https://s.click.aliexpress.com/e/_DdljyRf>

**Mounts Model By MapleLeafMakers**: <https://www.printables.com/model/408214-matchstick-diffusers>

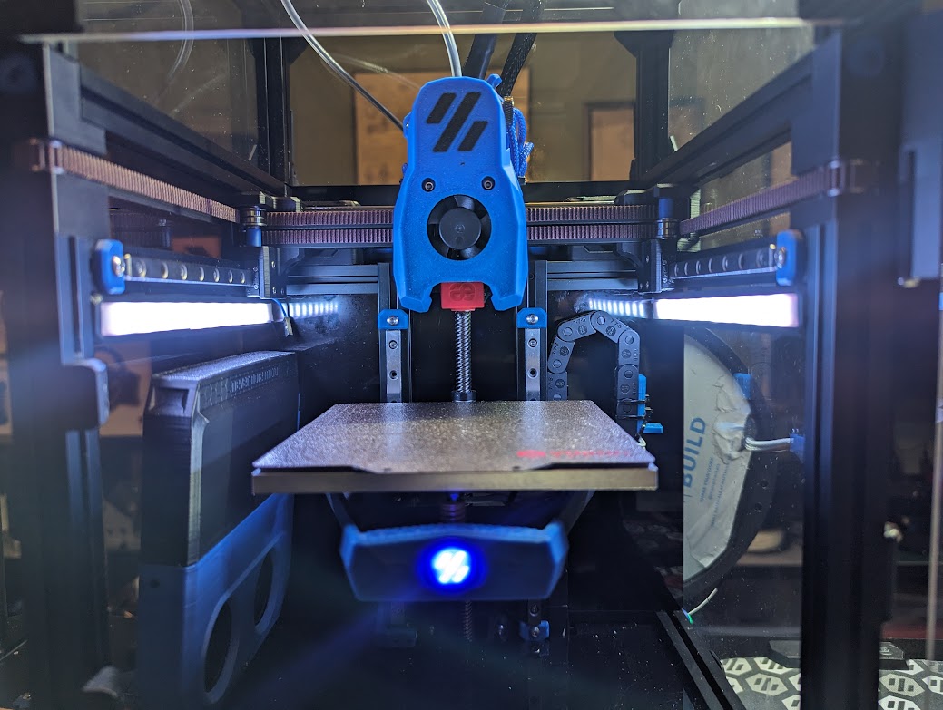
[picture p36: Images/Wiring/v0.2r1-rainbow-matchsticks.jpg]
Rainbow Matchsticks


Becuase RGB LEDs

### Rainbow Barf LED Skirts

**Product Links**:

- **Fabreeko**: <https://www.fabreeko.com/products/rainbow-leds-pcb-by-whoppingpochard?_pos=1&_sid=cb992e68d&_ss=r>
- **West3D**: <https://west3d.com/products/steathburner-led-upgrade-rgbw?_pos=1&_sid=57e17111c&_ss=r>
- **DFH**: <https://dfh.fm/products/rainbow-barf-led-pcb-by-whoppingpochard-and-vinnycordeiro>

**Model Links**:

- **Mounts Model By MapleLeafMakers**: <https://www.printables.com/model/408741-v0-rgb-skirt-logo>

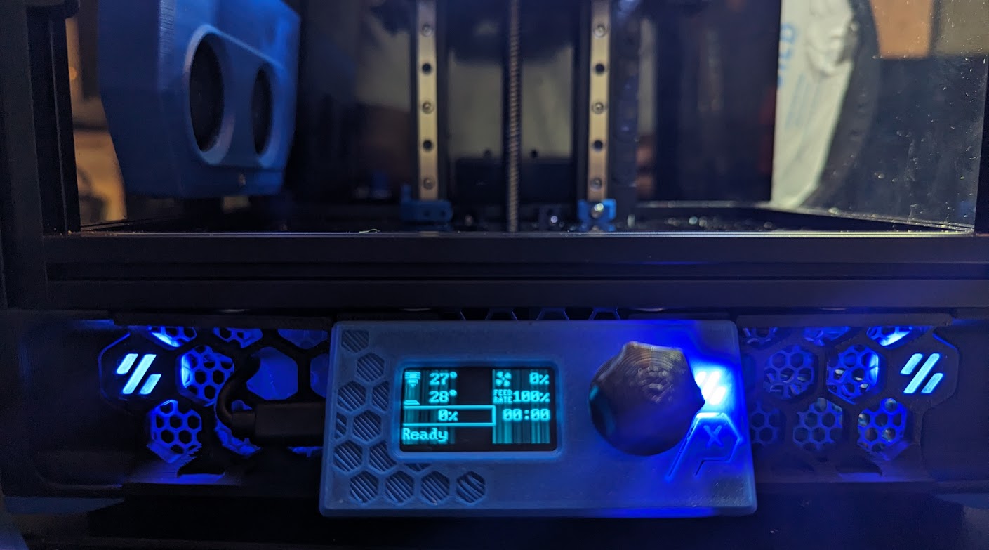
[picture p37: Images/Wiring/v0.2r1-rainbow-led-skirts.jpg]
Rainbow LED Skirts


### Oriber Smart Filament Runout Sensor

**Orbiter Extruder Project Link**: <https://www.orbiterprojects.com/orbiter-filament-sensor/>

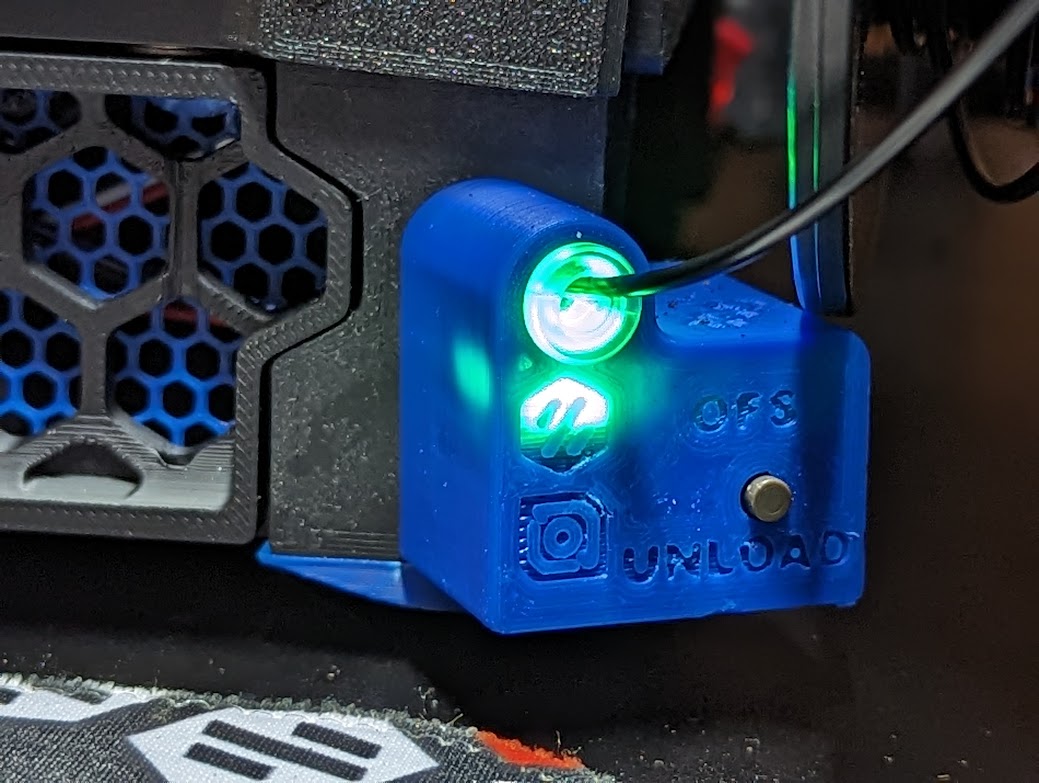
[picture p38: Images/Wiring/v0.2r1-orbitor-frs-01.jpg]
V0 Orbitor FRS


I thought it would be fun to modify the stock V0.2r1 FRS foot and use a smart sensor instead. With the use of a ball bearing and 2 push buttons the Orbiter sensor takes advantage of Klipper Macros to allow features like pausing/resuming, auto extruder heating, auto purging and quick unloading with the press of a button.

**My V0 Orbiter Foot Model [WIP]**: <https://www.printables.com/model/602670-voron-v02r1-foot-orbiter-filament-sensor-wip>

**Product Links**:

- **Ali Sensor**: <https://s.click.aliexpress.com/e/_DeiGEDb>
- **KB3D Sensor**: <https://kb-3d.com/store/probes-switches/825-ldo-orbiter-v1-15-filament-sensor-kit-v22-1652646845812.html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>
- **West3D**: <https://west3d.com/products/orbiter-filament-sensor-complete-kit-for-orbiter-extruder-v20-by-ldo-motors>
- **Fabreeko**: <https://www.fabreeko.com/products/orbiter-2-0-sensor?_pos=1&_sid=6352f305f>

## Mods Used

### Stealth Handles

These replace two of the side panel holders and offer a clean looking way to easily move the printer around

**Model Link By MapleLeafMakers** - <https://www.printables.com/model/481575-v0-stealth-handles>

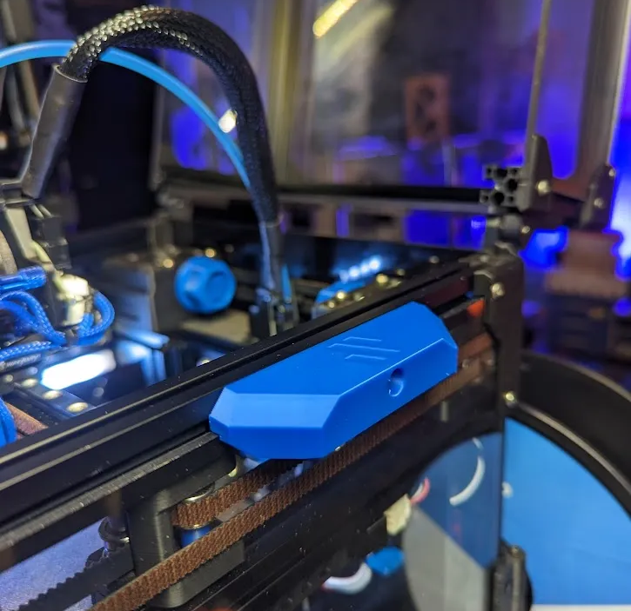
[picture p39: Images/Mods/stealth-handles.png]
Stealth Handles


### V0 Umbilical PTFE Guide + Molex Strain Relief

**Model Link** - <https://www.printables.com/model/404594-v0-umbilical-ptfe-guide-and-molex-strain-relief>

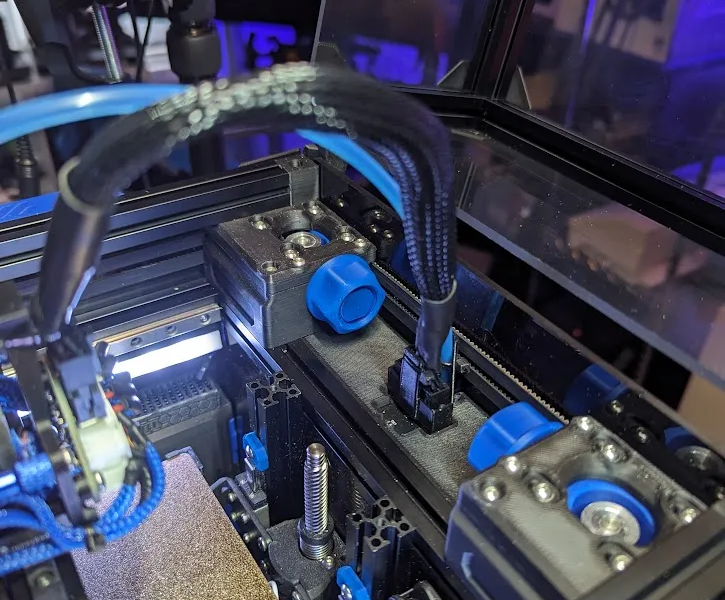
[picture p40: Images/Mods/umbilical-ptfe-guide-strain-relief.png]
PTFE Guide


### Bed Plate Guide

This is a little guide to make placing and aligning the PEI Bed Sheet easier.

**Model Link** - <https://www.printables.com/model/497212-voron-v01-pei-sheet-positioning-jig>

Bed Aligners

### Cable Management Tracks

These are printable versions of the tracks that LDO and other kits include.
I recomend printing them in PETG or a similar material that can flex a bit before snapping. I tried printing them in sever ABSs including Fusion Deep Water blue and the guide fingers were very brittle.

**Voron User Mod Link**: <https://mods.vorondesign.com/detail/YTmSPTcWpctfTKQj3bOPg>

Cable Managment Ducts 1

Cable Management Ducts 2

### V0 Hinged Spool holder and Rear Panel

**Mod Link**: <https://www.printables.com/model/548771-voron-0-hinged-back-panel-w-hinged-filament-spool->

I found that I was frequently taking off the rear panel and often had to lay the printer on its back. This combo of mods makes it easy to work on the electronics of the printer and move it around without undoing a lot of screws.

## Vector3D V0 Assembly Jigs

**Link**: <https://github.com/AdamV3D/V3D-Voron-Mods/tree/main/v0/Assembly%20Jigs/STL>

I found these Jigs by Adam from Vector3D very helpful. There are some for spacing elements like the linear rails when attaching them to the extrusion.

V3D Jigs 01

There's also jigs for spacing the Pulleys on the A/B Motor shafts which I found easier than the stock Voron tool

V3D Jigs 02

## Tuning

To tune the printer I used a combination of:

- The Klipper Config Checks: <https://www.klipper3d.org/Config_checks.html>
- Voron Guide Startup Checks: <https://docs.vorondesign.com/build/startup/>
- Voron Sensorless Setup: <https://docs.vorondesign.com/community/howto/clee/sensorless_xy_homing.html>
- Andrew Ellis' Tuning guide: <https://ellis3dp.com/Print-Tuning-Guide/>
- OrcaSlicer's Calibration Prints/Tools: <https://github.com/SoftFever/OrcaSlicer/wiki/Calibration>
- CNC Kitchen Max Volumetric Flow Rate Test: <https://hotend-flow-tester.netlify.app/>

Things to tune

- Extruder Rotation Distance (Ellis)
- Build surface prep (Ellis)
- First slayer Squish (Ellis)
- Pressure Advance (Ellis/OrcaSlicer)
- Tuned EM/Flow-Ratio for the main filaments I use (Ellis/OrcaSlicer)
  - Polymaker ABS/ASA
  - MH Build PLA
  - MH Build ABS
  - Fusion Heavy water Blue
- Retraction (Ellis/Orca)
- Max Volumetric Flow Rate (Ellis/OrcaSlicer/CNC Kitchen)
- Motor Currents (Ellis)
- Input shaper (Klipper Docs)
  - Axes Ressonance
  - Belt Tension
  - **Ali Fysetc Portable Input Shaper** - <https://s.click.aliexpress.com/e/_DeZPSbP>

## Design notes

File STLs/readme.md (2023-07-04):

# NOTE: For most up to date files be sure to check the individual GitHubs/Docs for the specific mod and download all necessary files for your V0 version (V0, V0.1, V0.2, V0.2r1, etc...)
# BTT PI
The BTT Pi has a different screw footprint than a standard Pi.

There are numerous DIN Cleat mounts for this.
This is from user RoCry on Printables: https://www.printables.com/model/476190-btt-bigtreetech-pi-mount

# Kirigami
The Kirigami frame from Formbot is a bit thicker (~2.5mm) than other frames. As such the frame won't fit into some of the standard Kirigami pieces. Specifically the Stealth version of the Nut Block and the V0.2 Chain Mount.

# V0 Umbilical

# V0 Display

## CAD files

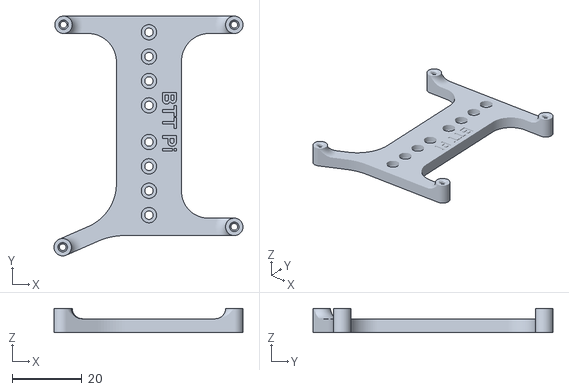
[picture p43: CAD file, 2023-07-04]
STLs/BTT Pi/BTT Pi.stl
54.2 x 68.8 x 7.00

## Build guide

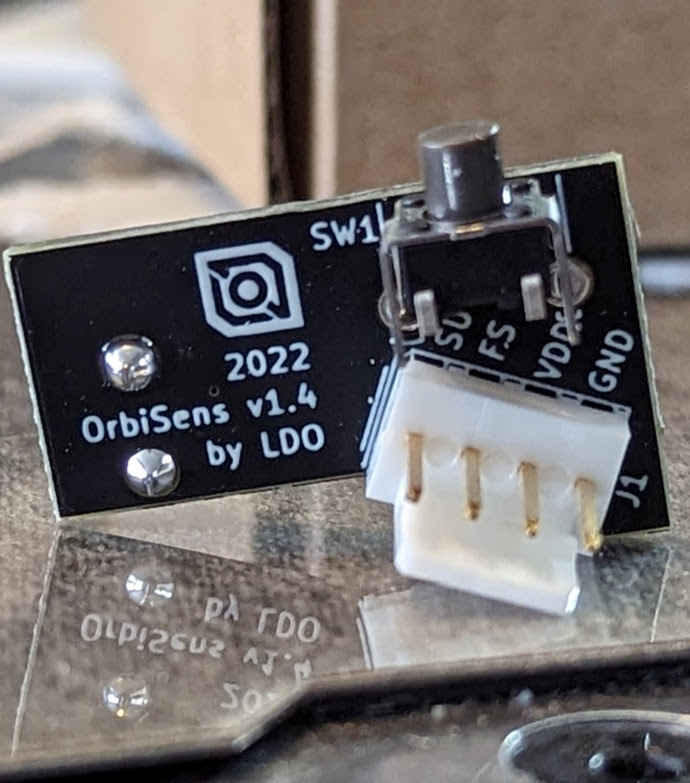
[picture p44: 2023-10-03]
Images/Wiring/v0.2r1-ldo-orbitor-frs.jpg

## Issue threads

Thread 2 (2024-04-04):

Dead links for remixed kirigami STLs

manisto, 2024-04-04:
I'm sorry for creating an issue for this, but I didn't know how else to contact you. The links for the remixed STLs for the kirigami bed on Printables are dead. I'm having the same issue as you, with the Z axis nut block fitting too tight, making the frame flex just enough that it doesn't run smoothly. If you have a local copy of those STLs, I would be very happy if you would add them to the `stl` folder of this repo.

SrgntBallistic, 2024-04-04:
Thanks for being this to my attention.

I'll look at the links. Putting them in the STLs folder is tough because they can get out of date if the original creator updates them.

But in this case it might be ok.

SrgntBallistic, 2024-04-04:
Looks like the model creator removed the files from Printables. I don't know why. I will see if I have them downloaded on a computer and upload them here.

If I can't find them I will try to recreate them

manisto, 2024-04-07:
All right, so I decided to take up the challenge and modify the STEP file for the nut block myself. I've made a parametric model, and am currently printing four variations. They should each accommodate a thickness of the frame for 2.1mm, 2.2mm, 2.3mm and 2.4mm, respectively. If they do the trick, I will upload them to Printables.

SrgntBallistic, 2024-04-08:
@manisto lmk if you get them uploaded! I'll do a test print and provide any feedback I can on my extra formbot bed frame. And replace the existing links/credit on GH!

Thanks

SrgntBallistic, 2024-10-16:
@manisto I updated the readme and included a link to your model. I rated it and uploaded a make. Thanks for the contributions

Closed 2024-10-16.

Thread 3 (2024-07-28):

Bed wiring

Carlsans, 2024-07-28:
The kit that I have received now has the thermal fuse wired in series so you got only 2 wires out of the bed + the themistor. All you need is a tie wrap to secure the wires, not need for an extra mount. Thanks a lot for your work, it helped me a lot 👍

SrgntBallistic, 2024-10-16:
Noted this in the readme. Thanks for the info!

Closed 2024-10-16.

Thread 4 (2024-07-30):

Fan connectors reversed polarized

Carlsans, 2024-07-30:
Two of the fans connectors from the umbilical to the board where wired in reverse. It caused the hotend fan and the blower not to work properly. Quick fix was to shave the end of one of the wire so it fit in reverse.

SrgntBallistic, 2024-10-16:
I've noted this in the readme. I did run into something similar in my build on one of the streams. I think I depinned the crimps and swapped them.

Carlsans, 2024-10-16:
Also, you already mentionned this but the hotend fan is extremely low
quality. It stopped working about after a week. It resulted in the hotend
mount meltdown, the hotend crashed into the bed scratching it badly. The
bed was bent and the x rail just unscrewed itself. It's a major issue.
I thought to myself that using the kit fan until I got my gdstime fan would
be a good idea, but no.
I now have a tach fan.

Le mer. 16 oct. 2024, à 15 h 37, Brian Rowe ***@***.***> a
écrit :

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

--

Carl Sansfaçon

Closed 2024-10-16.

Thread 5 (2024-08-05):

Fans are cheaper than I think

Carlsans, 2024-08-05:
This catastrophic failure is due to the hotend fan failure after less than a week of use. I also would not recommand using the mini stealthburner with the dragon hotend. Recommandation from the community : dragon burner hotend mount with sherpa mini extruder that use the same part except for 2 4010 blower fan. Buy GDSTime fans !!!!!!
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

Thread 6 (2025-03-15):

Typo in `max_accel` in the `[printer]` section?

Castdeath97, 2025-03-15:
`max_accel` seems to be set to 400 which is sub stock ender 3 accels and rather low for a V0, is this a typo?

SrgntBallistic, 2025-07-17:
> `max_accel` seems to be set to 400 which is sub stock ender 3 accels and rather low for a V0, is this a typo?

Yes this can be set to 2000-5000 out of the box. Not sure why it's at 400 here. But generally people will end up changing it as they go through Max Velocity/Accels tests and Input Shaper. I'll change it.

Closed 2025-07-17.

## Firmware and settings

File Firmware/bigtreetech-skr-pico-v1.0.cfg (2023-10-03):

[include mainsail.cfg]
# This file contains common pin mappings for the BIGTREETECH SKR Pico V1.0
# To use this config, the firmware should be compiled for the RP2040 with
# USB communication.

# The "make flash" command does not work on the SKR Pico V1.0. Instead,
# after running "make", copy the generated "out/klipper.uf2" file
# to the mass storage device in RP2040 boot mode

## Voron Design VORON 0.2 SKR Pico V1.0 config

## *** THINGS TO CHANGE/CHECK: ***
## MCU path                                                                     [mcu] section
## Z and Extruder motor currents                                                [tmc2209 stepper_*] sections. Uncomment the stepper motor you have
## Full steps per rotation for Extruder                                         [extruder] section
## Thermistor types                                                             [extruder] and [heater_bed] sections - See https://www.klipper3d.org/Config_Reference.html#common-thermistors for common thermistor types
## Motor currents                                                               [extruder] [stepper] and [_HOME_X/Y] macro sections
## PID tune                                                                     [extruder] and [heater_bed] sections
## Fine tune E steps                                                            [extruder] section
## For more info                                                                check https://docs.vorondesign.com/build/startup/#v0

[mcu]
#####################################################################
# Obtain definition by "ls -l /dev/serial/by-id/"
#####################################################################
serial: /dev/serial/by-id/usb-Klipper_rp2040_REPLACE_WITH_YOUR_VALUE
## serial: /dev/ttyAMA0 											# for UART connection
restart_method: command


[temperature_sensor mcu_temp]
sensor_type: temperature_mcu
min_temp: 0
max_temp: 100

[temperature_sensor btt_pi]
sensor_type: temperature_host
min_temp: 10
max_temp: 100

[printer]
kinematics: corexy
max_velocity: 500
max_accel: 400
max_z_velocity: 15
max_z_accel: 300
square_corner_velocity: 6.0

#####################################################################
#      X/Y Stepper Settings
#####################################################################

[stepper_x]
step_pin: gpio11
## Refer to https://docs.vorondesign.com/build/startup/#v0
dir_pin: gpio10                                                     # Check motor direction in link above. If inverted, add a ! before gpio10
enable_pin: !gpio12
rotation_distance: 40
microsteps: 32
full_steps_per_rotation: 200                                        # Set to 400 for 0.9° degree stepper motor, 200 is for 1.8° stepper motors
endstop_pin: tmc2209_stepper_x:virtual_endstop
position_endstop: 120
position_max: 120
homing_speed: 20                                                    # for sensorless homing it is recommended not to go above 40mm/s   
homing_retract_dist: 0
homing_positive_dir: true

[tmc2209 stepper_x]
uart_pin: gpio9
tx_pin: gpio8
uart_address: 0
interpolate: False
# you need to calculate the run_current value using the equation (rated_motor_current * 0.707 = Maximum_run_current) start with a value that is about 60%-70% of your maximum value.
# rated_motor_current * 0.707 * 65% = 1.5A * .707 * .65 = 0.69
run_current: 0.69           
sense_resistor: 0.110
stealthchop_threshold: 0                                            # Set to 999999 to turn stealthchop on, and 0 to use spreadcycle
diag_pin: ^gpio4    												# YOU NEED TO JUMP THIS DIAG PIN ON YOUR BOARD FOR SENSORLESS HOMING TO WORK 
driver_SGTHRS: 255  												# this is set to 255 which is the MAX sensitivity for sensorless homing, you will need to tune this later

[stepper_y]
step_pin: gpio6
## Refer to https://docs.vorondesign.com/build/startup/#v0
dir_pin: gpio5                                                      # Check motor direction in link above. If inverted, add a ! before gpio5
enable_pin: !gpio7
rotation_distance: 40
microsteps: 32
full_steps_per_rotation: 200                                        # Set to 400 for 0.9° degree stepper motor, 200 is for 1.8° stepper motors
endstop_pin: tmc2209_stepper_y:virtual_endstop
position_endstop: 120
position_max: 120
homing_speed: 20                                                    # for sensorless homing it is recommended not to go above 40mm/s   
homing_retract_dist: 0
homing_positive_dir: true

[tmc2209 stepper_y]
uart_pin: gpio9
tx_pin: gpio8
uart_address: 2
interpolate: False
# you need to calculate the run_current value using the equation (rated_motor_current * 0.707 = Maximum_run_current) start with a value that is about 60%-70% of your maximum value.
# rated_motor_current * 0.707 * 65% = 1.5A * .707 * .65 = 0.69
run_current: 0.69
sense_resistor: 0.110
stealthchop_threshold: 0                                            # Set to 999999 to turn stealthchop on, and 0 to use spreadcycle
diag_pin: ^gpio3    												# YOU NEED TO JUMP THIS DIAG PIN ON YOUR BOARD FOR SENSORLESS HOMING TO WORK 
driver_SGTHRS: 255  												# this is set to 255 which is the MAX sensitivity for sensorless homing, you will need to tune this later

#####################################################################
#   Z Stepper Settings
#####################################################################

[stepper_z]
step_pin: gpio19
dir_pin: !gpio28                                                    # Remove the ! before gpio28 if motor direction is inverted.
enable_pin: !gpio2
rotation_distance: 8                                                # For T8x8 integrated lead screw
microsteps: 32
endstop_pin: ^gpio25
position_endstop: 120
position_max: 120
position_min: -1.5
homing_speed: 20
second_homing_speed: 3.0
homing_retract_dist: 3.0


[tmc2209 stepper_z]
uart_pin: gpio9
tx_pin: gpio8
uart_address: 1
interpolate: False
## Formbot Moons 
# rated_motor_current * 0.707 * .65 = 0.65 * 0.707 * 0.65 = 0.30
run_current: 0.30
sense_resistor: 0.110
stealthchop_threshold: 0                                            # Set to 999999 to turn stealthchop on, and 0 to use spreadcycle

#####################################################################
#   Extruder
#####################################################################

[extruder]
step_pin: gpio14
dir_pin: gpio13                                                     # Add ! if moving opposite direction
enable_pin: !gpio15
#full_steps_per_rotation: 200                                       # Set to 200 for LDO 1.8° stepper motor, and set to 400 for OMC(StepperOnline) 0.9° stepper motor
rotation_distance: 22.23                                            # See calibrating rotation_distance on extruders doc
gear_ratio: 50:10                                                   # For Mini Afterburner
microsteps: 32
nozzle_diameter: 0.400
filament_diameter: 1.750
heater_pin: gpio23
## Check what thermistor type you have. See https://www.klipper3d.org/Config_Reference.html#common-thermistors for common thermistor types.
## Use "Generic 3950" for NTC 100k 3950 thermistors
sensor_type: ATC Semitec 104NT-4-R025H42G                            # default Formbot CHC V6
sensor_pin: gpio27
control: pid                                                        # Do PID calibration after initial checks
pid_Kp: 28.182
pid_Ki: 1.978
pid_Kd: 100.397
min_temp: 0
max_temp: 270
min_extrude_temp: 170
max_extrude_only_distance: 150
max_extrude_cross_section: 0.8
pressure_advance: 0.0                                               # See tuning pressure advance doc
pressure_advance_smooth_time: 0.040

[tmc2209 extruder]
uart_pin: gpio9
tx_pin: gpio8
uart_address: 3
interpolate: False
## For Formbot Moons
# rated_motor_current * 0.707 * .65 = 1 * 0.707 * 0.65 = 0.46
run_current: 0.46
sense_resistor: 0.110
stealthchop_threshold: 0                                            # Set to 0 for spreadcycle, avoid using stealthchop on extruder

#####################################################################
#   Bed Heater
#####################################################################

[heater_bed]
heater_pin: gpio21
## Check what thermistor type you have. See https://www.klipper3d.org/Config_Reference.html#common-thermistors for common thermistor types.
## Use "Generic 3950" for Keenovo heaters
sensor_type: Generic 3950
sensor_pin: gpio26
smooth_time: 3.0
#max_power: 0.6                                                     # Only needed for 100w pads
min_temp: 0
max_temp: 120
control: pid                                                        # Do PID calibration after initial checks
pid_kp: 68.453
pid_ki: 2.749
pid_kd: 426.122

#####################################################################
# Fan Control
#####################################################################
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

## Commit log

2023-07-04 initial commitof files and readmes
    [BTT Pi.stl, bigtreetech-skr-pico-v1.0.cfg]
2023-07-04 feat: kirigami bed github
2023-07-04 Update README.md
    Add Cable Manage tracks to readme
2023-10-03 feat: update readme and default printer.cfg
    [bigtreetech-skr-pico-v1.0.cfg]
2023-10-03 feat: add wiring diagram
2023-10-03 feat: wiring images in readme
2023-10-12 feat: gen wiring diagram, bed stuff
2023-10-12 feat: wiring and kirigami features
2023-10-12 fix: wiring image fan switch
2023-10-24 feat: motor drawings/data, usb cable, tuning info
2023-11-25 feat: remixed chain mount
2023-12-25 feat: add video link, printer.cfg details, other info
2023-12-27 fix: fan lines & names
2024-01-03 feat: add UART wiring/instructions
2024-03-06 feat: extrusion and no drop nut info
2024-10-16 Update README.md - add manisto's nut block link
2024-10-18 feat: add link to klipper auto backup github repo
